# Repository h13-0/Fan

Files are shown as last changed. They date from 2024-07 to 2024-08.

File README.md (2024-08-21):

# PD快充风扇
特性：
- 供电支持Type-C PD快充协议和DC 12V直流供电。
- 可调转速，可自选高风速和静音模式，转速调节精度为300档，按下旋钮即可满速。
- 核心主控使用STM8，Release界面有编译完成的二进制文件，无需配置IDE即可刷入

## 实物图


## 电路图
26Pin版本电路图如下：  
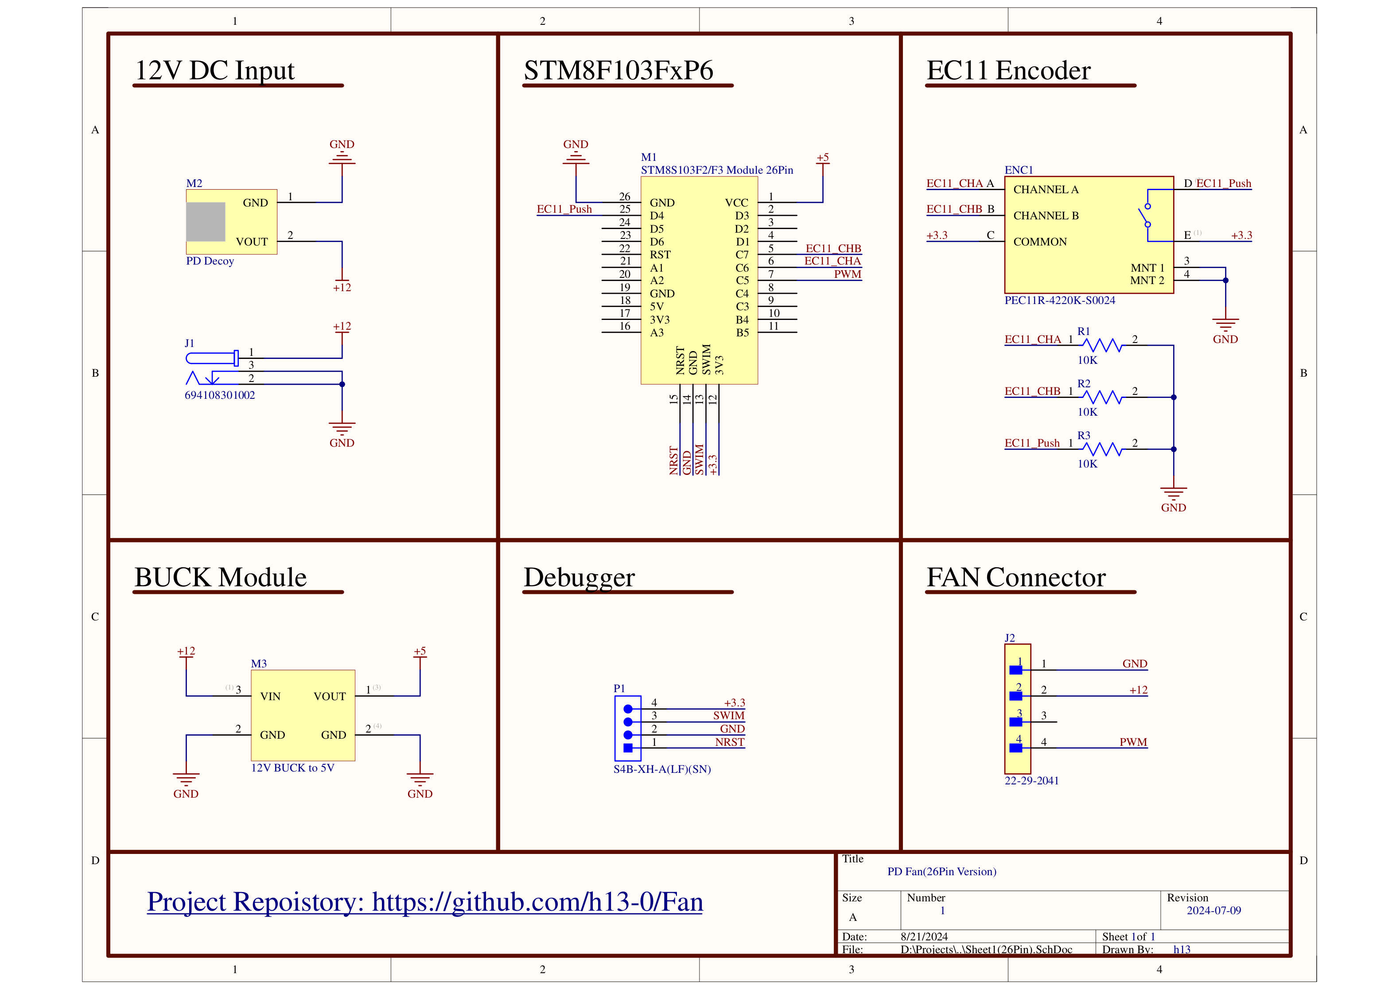
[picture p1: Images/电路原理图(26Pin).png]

PCB工程文件见目录[PCB](https://github.com/h13-0/Fan/tree/master/PCB)：
- 26Pin版本工程文件为[FAN_PCB(26Pin).PrjPcb](https://github.com/h13-0/Fan/blob/master/PCB/FAN_PCB(26Pin).PrjPcb)，PCB文件为[PCB1(26Pin).PcbDoc](https://github.com/h13-0/Fan/blob/master/PCB/PCB1(26Pin).PcbDoc)
- 28Pin版本工程文件为[FAN_PCB(28Pin).PrjPcb](https://github.com/h13-0/Fan/blob/master/PCB/FAN_PCB(28Pin).PrjPcb)，PCB文件为[PCB1(28Pin).PcbDoc](https://github.com/h13-0/Fan/blob/master/PCB/PCB1(28Pin).PcbDoc)
PCB尺寸统一为74mm\*25mm，孔位见PCB丝印。

## 外壳模型
外壳模型使用SolidWorks2024建模，有导出[STL文件](./Shell/外壳.STL)，使用3D打印即可完成制作。  
如需适配其他型号的80mm风扇，可基于上述建模修改或根据PCB丝印所标识的尺寸信息重新绘制。  

## 注意事项
市售的STM8S103FxP6的最小系统板有两个版本，分别为26Pin和28Pin，推荐使用26Pin版本，该版本较为常用。  
两个版本区别如下图所示：  

（上为26Pin，下为28Pin）

## 程序刷入方法(无需IDE)
1. 获取[STVP-STM8](https://www.st.com.cn/zh/development-tools/stvp-stm8.html#st-get-software)
2. 打开STVP，依次进行如下操作：
    1. 配置调试器和目标芯片：
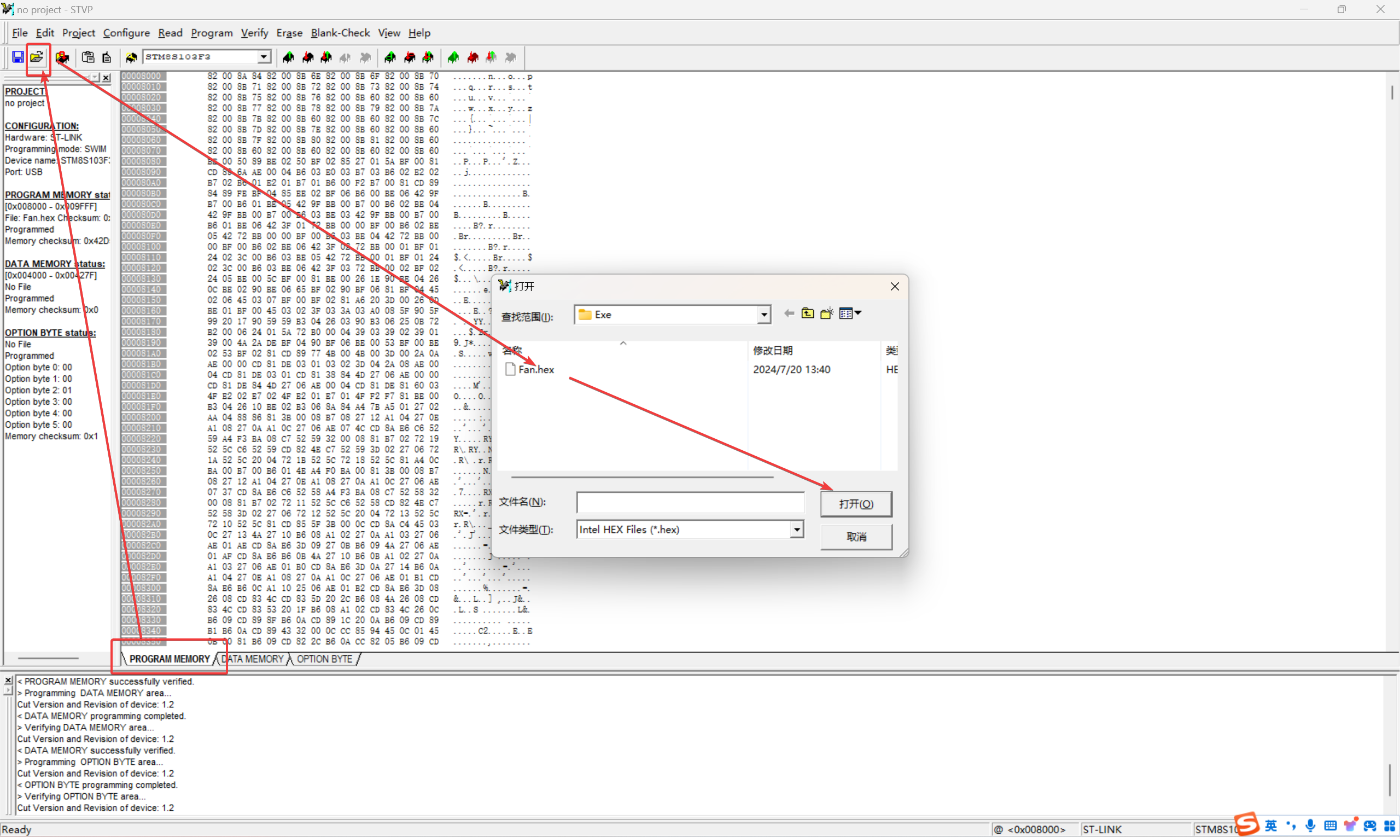
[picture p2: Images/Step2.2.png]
    2. 在 `PROGRAM MEMORY` 页面打开 [Release]() 中压缩包中的 `Fan.hex` 
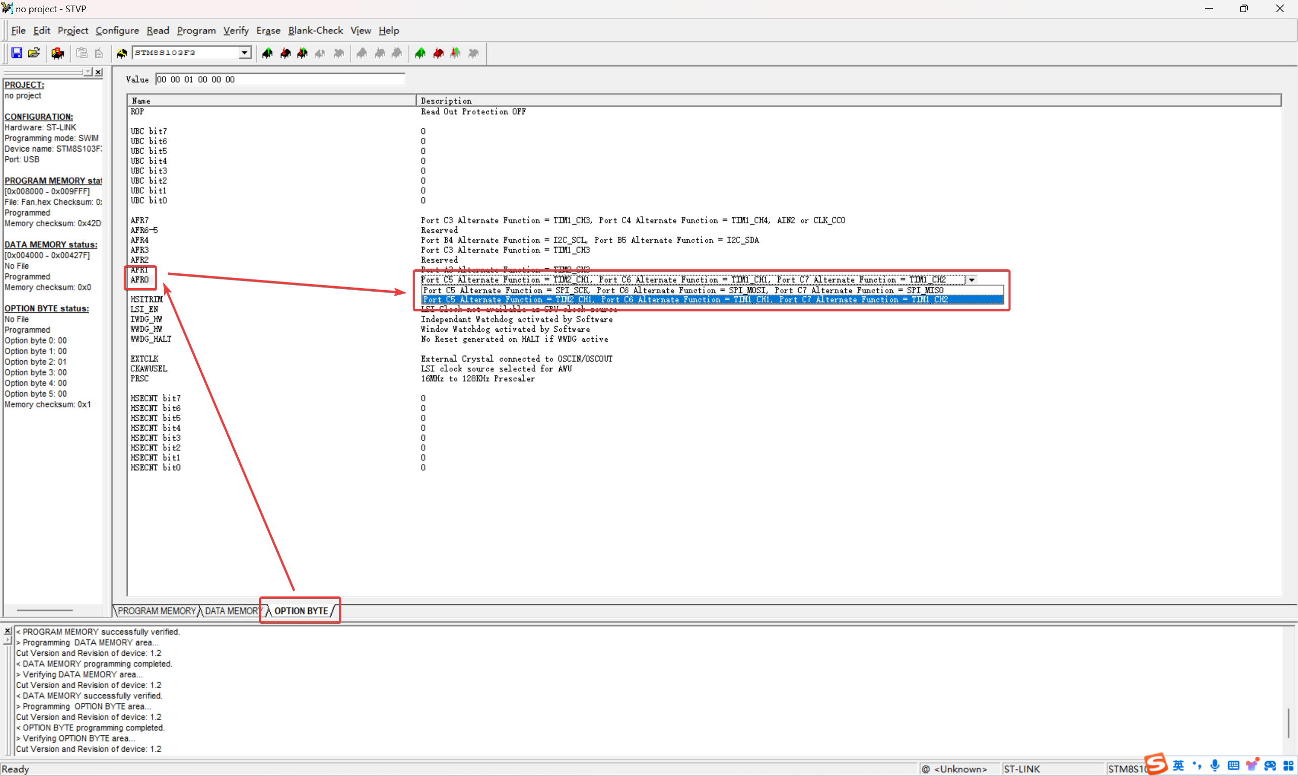
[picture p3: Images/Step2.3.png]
    3. 在 `OPTION BYTE` 页面将 `AFR0` 配置为使能 TIM1_CH1 和 TIM1_CH2：
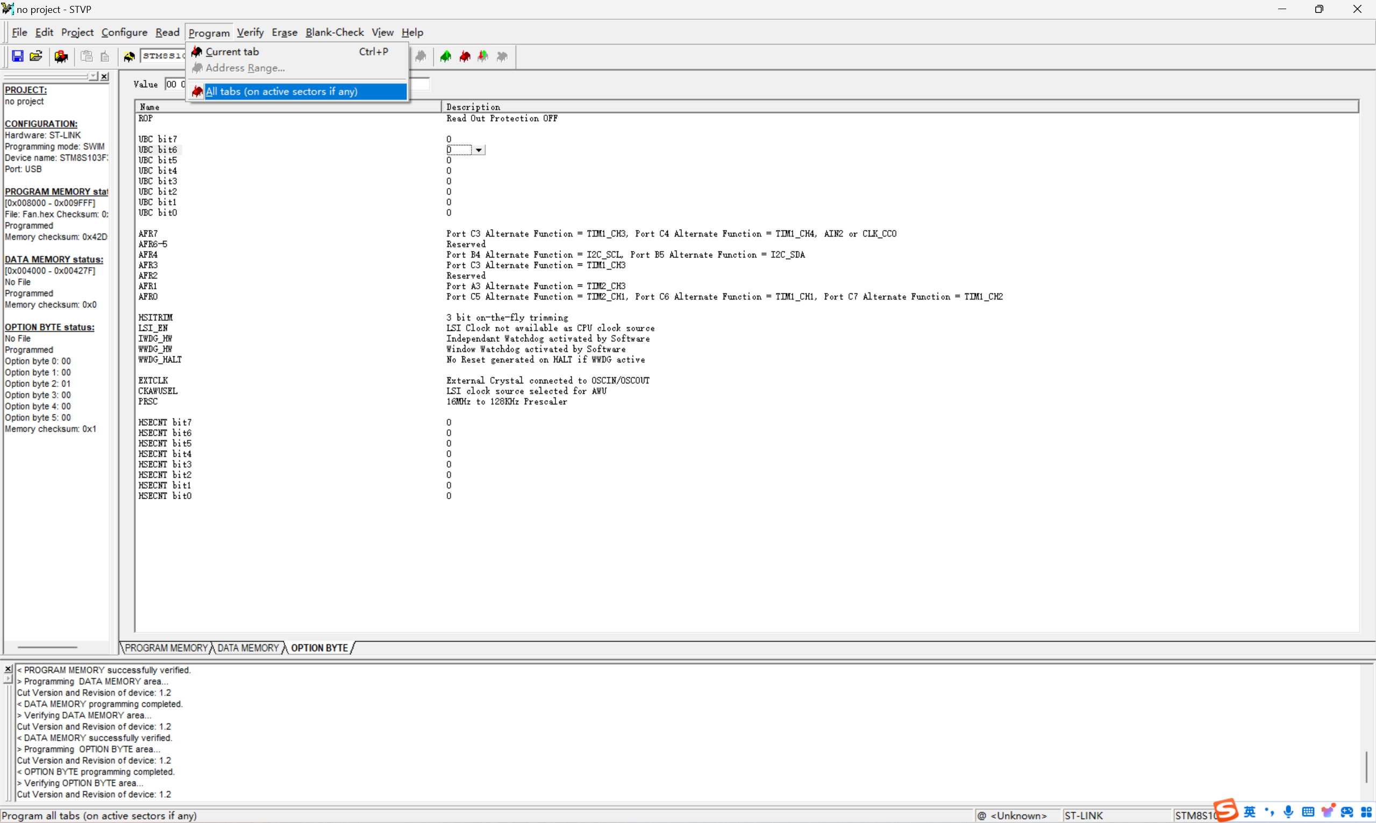
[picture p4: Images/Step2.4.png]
    4. 在工具栏 `Program` 点击 `All tabs` 将固件和配置下载到STM8FxP6单片机中：

## BOM

| 物料名称 | 参数/型号 | 数量 | 购买链接 |
| --- | --- | ---- | --- |
| 80mm服务器风扇 | 8038 三洋 12V 1.8A | 1 | https://item.taobao.com/item.htm?spm=a1z09.2.0.0.3a172e8dN2QdaD&id=12923471278&_u=a2ncf4788bf0  |
| 80mm风扇网罩 | | 1-2  | https://item.taobao.com/item.htm?spm=a1z09.2.0.0.67002e8dZDwEzv&id=652052250420&_u=a2ncf478591d |
| STM8S103F3P6最小系统板 | 26Pin版本 | 1 | https://item.taobao.com/item.htm?spm=a1z09.2.0.0.3a172e8drIuggJ&id=524863693731&_u=a2ncf4783ec0 |
| PD诱骗器 | 12V | 1 | https://item.taobao.com/item.htm?spm=a1z09.2.0.0.3a172e8drIuggJ&id=639940641909&_u=a2ncf478ed00 |
| DC降压模块 | 12V转5V | 1 | https://item.taobao.com/item.htm?spm=a1z09.2.0.0.67002e8dtGKmA8&id=560178970252&_u=a2ncf478929c |
| 3脚DC母座 | | 1 | https://item.taobao.com/item.htm?spm=a1z09.2.0.0.67002e8dtGKmA8&id=521786520463&_u=a2ncf478625b |
| EC11卧式编码器，带按钮  | 20脉冲/圈 | 1 | https://item.taobao.com/item.htm?spm=a1z09.2.0.0.67002e8dtGKmA8&id=7872903968&_u=a2ncf478e268 |
| 10K直插电阻 | AXIAL-0.4 | 3 | 略 |
| xh2.54 弯头座 | 4Pin | 1 | https://item.taobao.com/item.htm?spm=a1z09.2.0.0.67002e8d309Yz2&id=587341434964&_u=a2ncf478175b |
| 4Pin风扇座 | | 1 | 任选，可用排针代替 |
| M3螺丝 | 3-5mm长度即可 | 1 | 任选，固定PCB用 |
| M4螺丝 | 3-5mm长度即可 | 8 | 可能需要选配螺母，固定风扇网罩、外壳、风扇用，具体型号外观随意 |

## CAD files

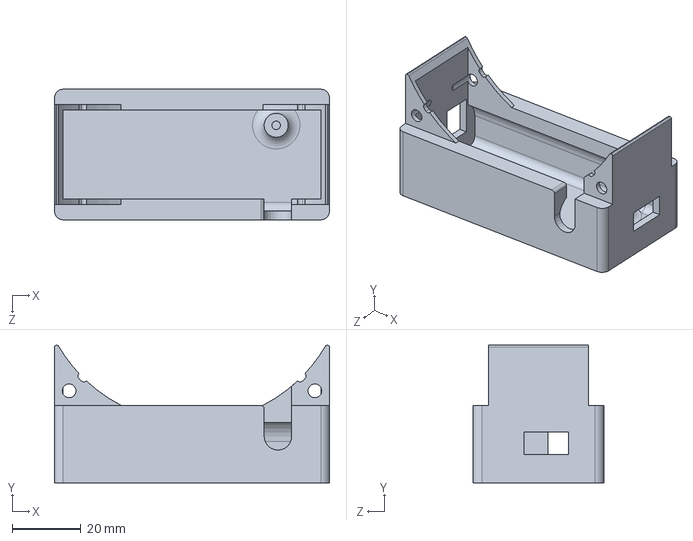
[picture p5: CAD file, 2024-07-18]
Shell/外壳.SLDPRT
80.0 x 40.0 x 38.0 mm

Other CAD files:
STM8/Project/FAN/STVD/Cosmic/stm8s007.stp
STM8/Project/FAN/STVD/Raisonance/stm8s208.stp
STM8/Project/FAN/STVD/Cosmic/stm8s105.stp
STM8/Project/FAN/STVD/Raisonance/stm8s105.stp
STM8/Project/FAN/STVD/Cosmic/stm8af52ax.stp
STM8/Project/FAN/STVD/Raisonance/stm8af52ax.stp
STM8/Project/FAN/STVD/Cosmic/stm8s003.stp
STM8/Project/FAN/STVD/Raisonance/stm8s903.stp
STM8/Project/FAN/STVD/Cosmic/stm8af626x.stp
STM8/Project/FAN/STVD/Raisonance/stm8af626x.stp
STM8/Project/FAN/STVD/Cosmic/stm8s103.stp
STM8/Project/FAN/STVD/Raisonance/stm8s207.stp
STM8/Project/FAN/STVD/Cosmic/stm8af622x.stp
STM8/Project/FAN/STVD/Raisonance/stm8s005.stp
STM8/Project/FAN/STVD/Cosmic/stm8s903.stp
STM8/Project/FAN/STVD/Raisonance/stm8s103.stp
STM8/Project/FAN/STVD/Cosmic/stm8s005.stp
STM8/Project/FAN/STVD/Cosmic/stm8af62ax.stp
STM8/Project/FAN/STVD/Cosmic/stm8s207.stp
STM8/Project/FAN/STVD/Cosmic/stm8s208.stp
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

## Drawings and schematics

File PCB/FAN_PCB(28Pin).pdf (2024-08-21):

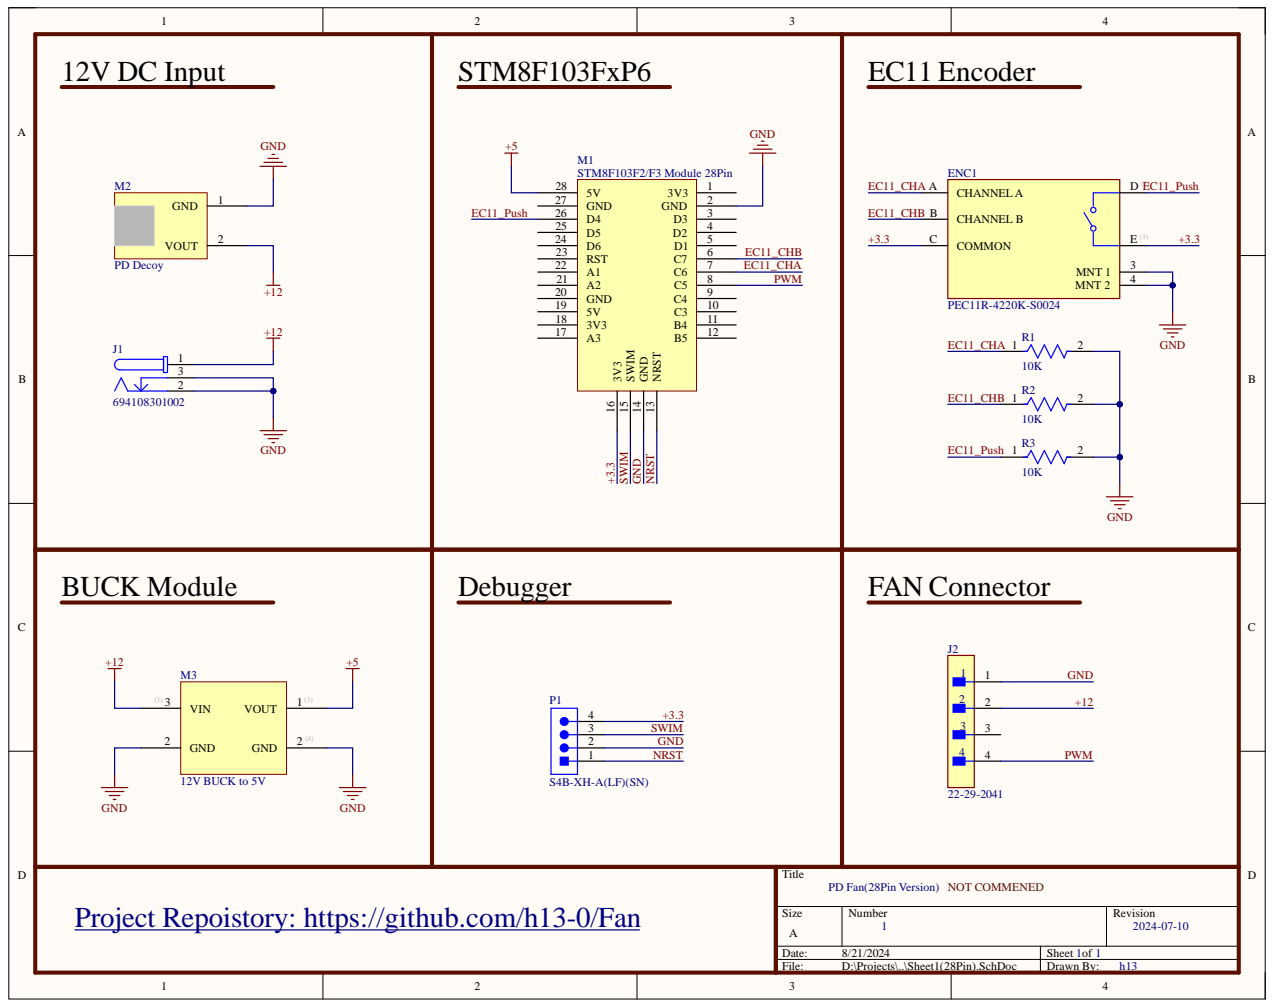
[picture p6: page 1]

Project Repoistory: https://github.com/h13-0/Fan | Title PD Fan(28Pin Version) NOT COMMENED

Size A | Number 1 | Revision 2024-07-10

Date: 8/21/2024 | Sheet of 1 1
File: D:\Projects\..\Sheet1(28Pin).SchDoc | Drawn By: h13

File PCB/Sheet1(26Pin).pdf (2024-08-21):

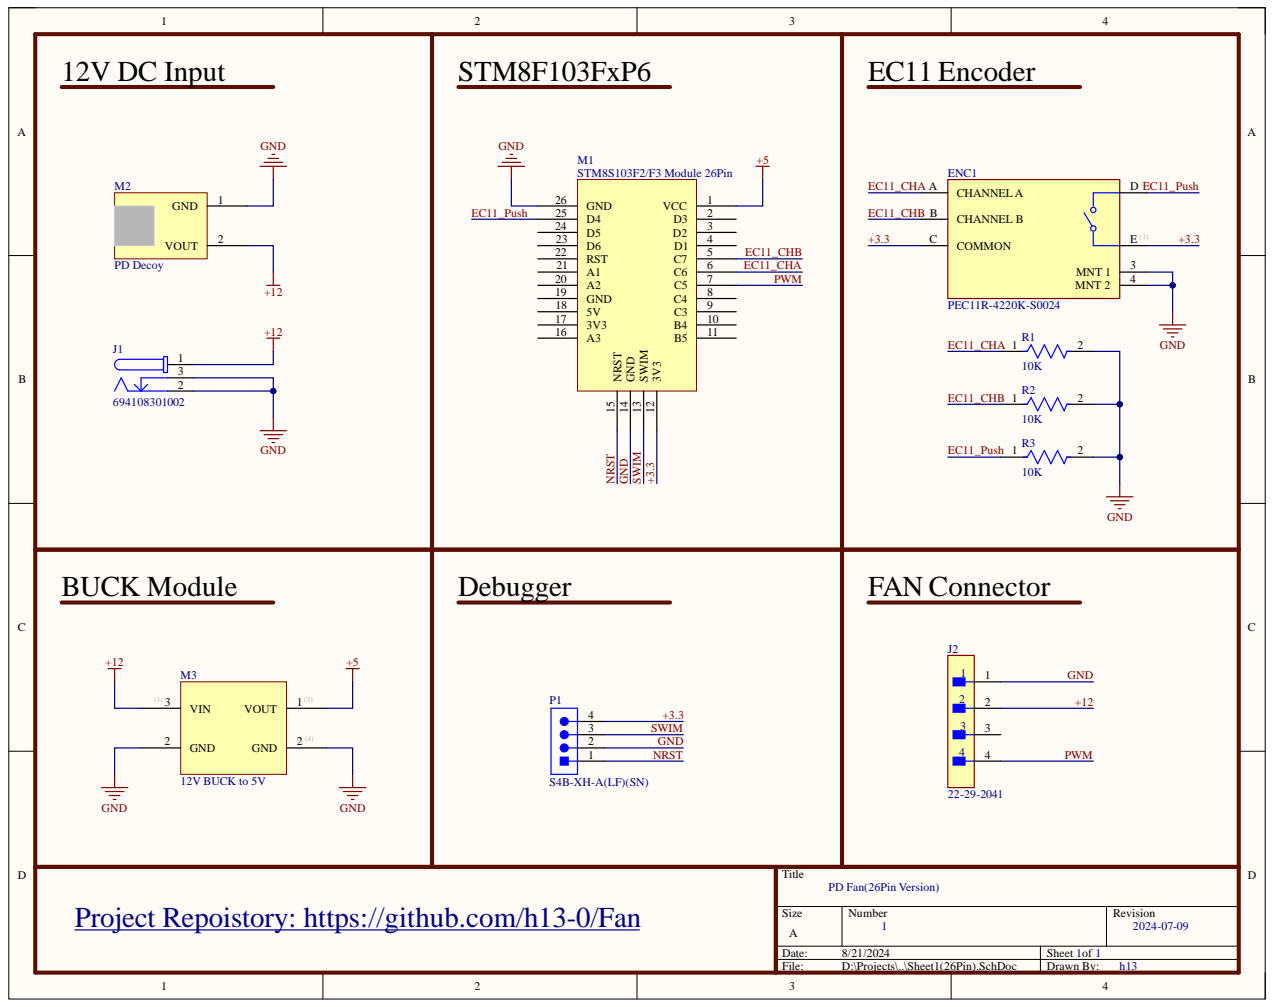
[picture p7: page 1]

Project Repoistory: https://github.com/h13-0/Fan | Title PD Fan(26Pin Version)

Size A | Number 1 | Revision 2024-07-09

Date: 8/21/2024 | Sheet of 1 1
File: D:\Projects\..\Sheet1(26Pin).SchDoc | Drawn By: h13

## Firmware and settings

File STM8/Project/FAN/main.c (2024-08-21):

/* Includes ------------------------------------------------------------------*/
#include "stm8s.h"
#include "stdio.h"

/* Private typedef -----------------------------------------------------------*/
/* Private define ------------------------------------------------------------*/

/* Private macro -------------------------------------------------------------*/
/* Private variables ---------------------------------------------------------*/
/* Private function prototypes -----------------------------------------------*/
/* Private functions ---------------------------------------------------------*/

/**
  * @brief  Configure TIM2 peripheral in PWM mode
  * @param  None
  * @retval None
  */
static void TIM2_Config(void)
{
  /* Time base configuration */
  TIM2_TimeBaseInit(TIM2_PRESCALER_16, 19999);

  /* PWM1 Mode configuration: Channel1 */ 
  TIM2_OC1Init(TIM2_OCMODE_PWM1, TIM2_OUTPUTSTATE_ENABLE, 0, TIM2_OCPOLARITY_HIGH);
  TIM2_CCxCmd(TIM2_CHANNEL_1, ENABLE);
  TIM2_OC1PreloadConfig(ENABLE);
  TIM2_ARRPreloadConfig(ENABLE);

  GPIO_Init(GPIOC, GPIO_PIN_5, GPIO_MODE_OUT_PP_HIGH_FAST);
  
  /* TIM2 enable counter */
  TIM2_Cmd(ENABLE);
}

static void GPIO_Config(void)
{
    GPIO_Init(GPIOD, GPIO_PIN_4, GPIO_MODE_IN_FL_NO_IT);
}

static void TIM1_Config(void)
{
    TIM1_DeInit();
    TIM1_TimeBaseInit(0,TIM1_COUNTERMODE_UP,65536-1,0);
    TIM1_ICInit((TIM1_Channel_TypeDef)(TIM1_CHANNEL_1 | TIM1_CHANNEL_2), TIM1_ICPOLARITY_RISING, TIM1_ICSELECTION_DIRECTTI, TIM1_ICPSC_DIV1, 0);
    TIM1_EncoderInterfaceConfig(TIM1_ENCODERMODE_TI12, TIM1_ICPOLARITY_RISING, TIM1_ICPOLARITY_RISING);
    TIM1_ClearFlag(TIM1_FLAG_UPDATE);
    TIM1_SetCounter(0);
    TIM1_Cmd(ENABLE);
}

static void sleepOneMilliseond(void)
{
    uint8_t Ms = 1;
    uint8_t j = 30;
	
    while( Ms-- )
    {
        while( j-- );
    }
}

void SleepMilliseonds( uint16_t MilliSeconds )
{
    while(MilliSeconds--)
    {
        sleepOneMilliseond();
    }
}

/**
  * @brief  Main program.
  * @param  None
  * @retval None
  */
void main(void)
{
    // Set clock to 16MHz.
    CLK_HSIPrescalerConfig(CLK_PRESCALER_HSIDIV1);
  
    // Init GPIO.
    // GPIO_Input -> Encoder Push (D4)
    GPIO_Config();
  
    // Init TIM2.
    // TIM2 -> PWM (C5)
    TIM2_Config();
  
    // TIM1 -> Encoder C6 C7.
    TIM1_Config();
  
    while(1)
    {
        if(!GPIO_ReadInputPin(GPIOD, GPIO_PIN_4))
        {
            int32_t count = 0;
            count = TIM1_GetCounter();
      
            if(count > 32768)
            {
                count = 65535 - count;
            } else {
                count = - count;
            }
      
            // 60 Pulses per turn.
            // 20% duty cycle per turn.
            if(count > 300)
            {
                TIM1_SetCounter(-300);
                count = 300;
            } else if(count < 0)
            {
                TIM1_SetCounter(0);
                count = 0;
            }
      
            uint16_t cmpValue = 20000 * count / 300;
            TIM2_SetCompare1(cmpValue);
        } else {
            TIM2_SetCompare1(20000);
        }
        SleepMilliseonds(100);
    }
}

#ifdef USE_FULL_ASSERT

/**
  * @brief  Reports the name of the source file and the source line number
  *   where the assert_param error has occurred.
  * @param file: pointer to the source file name
  * @param line: assert_param error line source number
  * @retval None
  */
void assert_failed(uint8_t* file, uint32_t line)
{ 
  /* User can add his own implementation to report the file name and line number,
     ex: printf("Wrong parameters value: file %s on line %d\r\n", file, line) */

  /* Infinite loop */
  while (1)
  {
  }
}
#endif

/**
  * @}
  */


/************************ (C) COPYRIGHT STMicroelectronics *****END OF FILE****/

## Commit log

2024-06-21 First commit.
    [FAN_PCB.PrjPcb, PCB1.PcbDoc, Sheet1.SchDoc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]
2024-07-08 Preliminary completion of circuit design
    [Sheet1.SchDoc]
2024-07-09 完成电路设计
    [FAN_PCB(26Pin).PrjPcb, FAN_PCB(28Pin).PrjPcb, FAN_PCB.PrjPcb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]
2024-07-10 完成外壳设计
    [PCB1(26Pin).PcbDoc, PCB1(28Pin).PcbDoc, 外壳.SLDPRT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]
2024-07-10 更新文档
2024-07-13 优化外壳尺寸
    [外壳.SLDPRT, 外壳.STL]
2024-07-18 修复外壳尺寸错误，修复bug
    [外壳.SLDPRT, 外壳.STL]
2024-08-21 修复bug
    [FAN_PCB(28Pin).PrjPcb, PCB1(26Pin).PcbDoc, PCB1(28Pin).PcbDoc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]
2024-08-21 更新实物图
